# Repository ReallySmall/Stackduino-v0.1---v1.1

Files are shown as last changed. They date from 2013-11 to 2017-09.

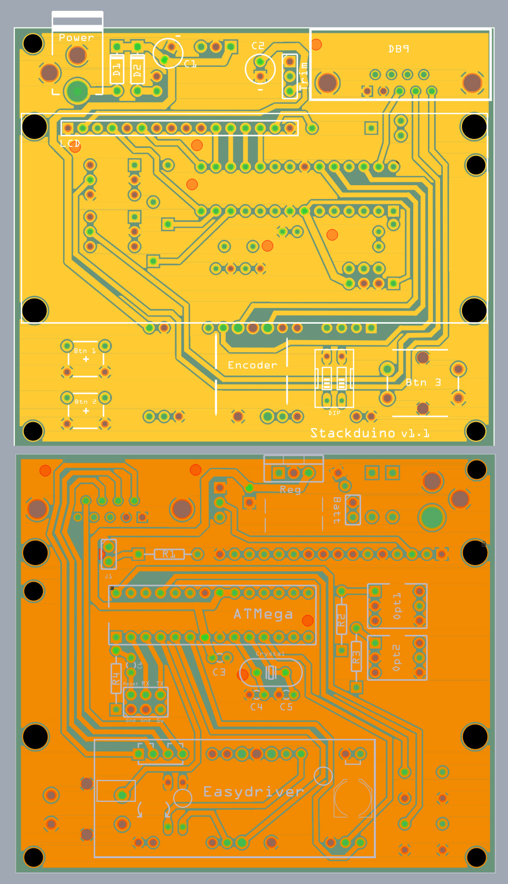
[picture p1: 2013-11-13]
Stackduino-v1.1-pcb-top-bottom-views.jpg

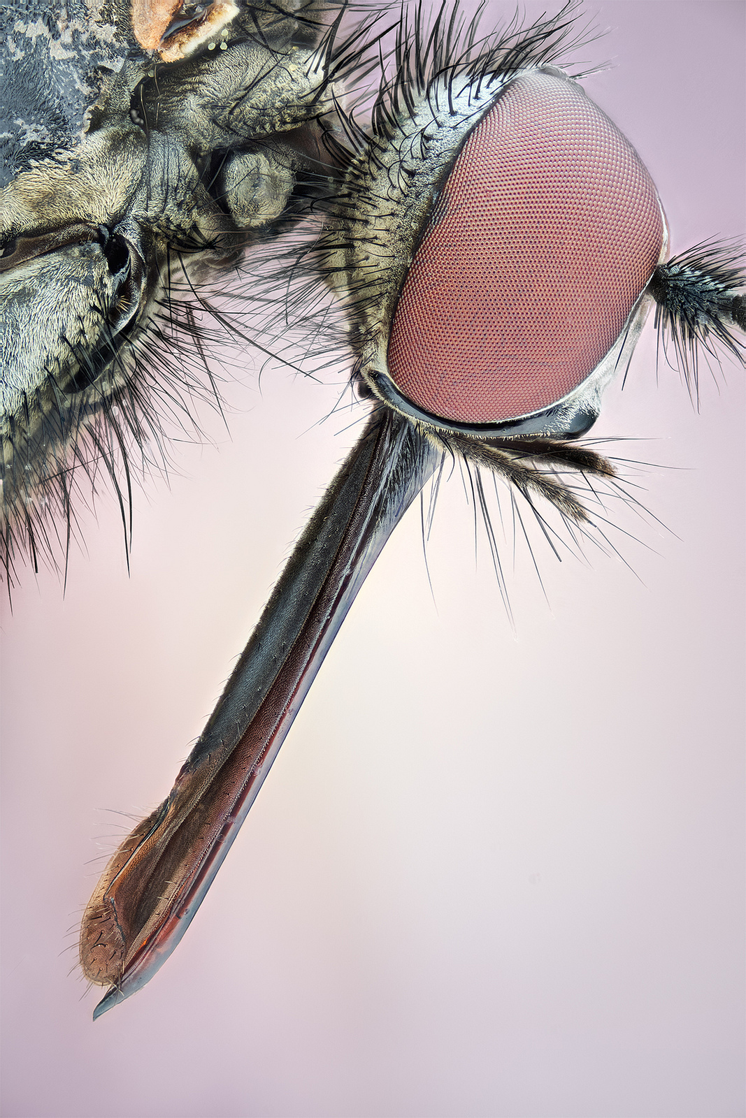
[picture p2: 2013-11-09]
Example image made with Stackduino.jpg

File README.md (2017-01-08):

Stackduino
==========
Please visit the project site for details: https://www.stackduino.net

Copyright 2017 Richard Iles

Permission is hereby granted, free of charge, to any person obtaining a copy of this software and associated documentation files (the "Software"), to deal in the Software without restriction, including without limitation the rights to use, copy, modify, merge, publish, distribute, sublicense, and/or sell copies of the Software, and to permit persons to whom the Software is furnished to do so, subject to the following conditions:

The above copyright notice and this permission notice shall be included in all copies or substantial portions of the Software.

THE SOFTWARE IS PROVIDED "AS IS", WITHOUT WARRANTY OF ANY KIND, EXPRESS OR IMPLIED, INCLUDING BUT NOT LIMITED TO THE WARRANTIES OF MERCHANTABILITY, FITNESS FOR A PARTICULAR PURPOSE AND NONINFRINGEMENT. IN NO EVENT SHALL THE AUTHORS OR COPYRIGHT HOLDERS BE LIABLE FOR ANY CLAIM, DAMAGES OR OTHER LIABILITY, WHETHER IN AN ACTION OF CONTRACT, TORT OR OTHERWISE, ARISING FROM, OUT OF OR IN CONNECTION WITH THE SOFTWARE OR THE USE OR OTHER DEALINGS IN THE SOFTWARE.

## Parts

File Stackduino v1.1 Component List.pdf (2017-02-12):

PCB Component Label | Component Name/ Value | Insert either way? | Notes
Power | DC Barrel Jack Connector | No | 2.1mm centre pole diameter
D1 | Schottky Diode 1A 40v | No | Diode OR power supply select
D2 | Schottky Diode 1A 40v | No | Diode OR power supply select
DB9 | Serial DB9 right angle pcb connector | No | Carries motor, camera and limit switch signals out of the board
C1 | Electrolytic Capacitor 100uF 16v | No | Power supply filtering
C2 | Electrolytic Capacitor 100uF 16v | No | Power supply filtering
C3 | Ceramic Capacitor 0.1uF | Yes | Reset pin
C4 | Ceramic Capacitor 22pf | Yes | Crystal
C5 | Ceramic Capacitor 22pf | Yes | Crystal
C6 | Ceramic Capacitor 0.1uF | Yes | For reset pin when transferring code
Reg | 5v Linear Regulator | No | Voltage regulator
Trim | 10k Trimpot | Yes | LCD contrast control
R1 | 220 Ohm 1/4 Watt Resistor LCD | Yes | LCD backlight
R2 | 220 Ohm 1/4 Watt Resistor | Yes | 4n35 resistor
R3 | 220 Ohm 1/4 Watt Resistor | Yes | 4n35 resistor
R4 | 1.5K Ohm 1/4 Watt Resistor | Yes | Reset pull-up resistor
Opt1 | 4n35 Opto-isolator | No | Camera signal isolation
Opt2 | 4n35 Opto-isolator | No | Camera signal isolation
ATMega | ATMega328 + DIP socket | No | The MCU
Crystal | 16Mhz Crystal | Yes | MCU clock
Easydriver | Easydriver v4.4 Stepper | No | Motor driver
Btn 1 | Mini push button switch | Yes | Manual control - forward
Btn 2 | Mini push button switch | Yes | Manual control - backward
Btn 3 | Push button switch 12mm | Yes | Main function button
Encoder | Standard rotary encoder with push button switch | No | Menu navigation and setting changes
DIP | DIP switch (2 channel) | No | For pulling Easydriver MS1 and MS2 pins high or low
(not labelled) | Male pcb header x 45 | Yes | About 45 male pcb headers needed throughout the board - standard 2.54 pitch

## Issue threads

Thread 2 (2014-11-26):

First image in stack should be taken before stage is moved

ReallySmall, 2014-11-26:
Currently stage moves the first slice distance and then the first image is taken - meaning what you see in the viewfinder/ live view is not quite what gets taken.

ReallySmall, 2017-06-11:
Resolved

Closed 2017-06-11.

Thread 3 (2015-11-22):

Stack not ending is Set Num  over 1

cru67, 2015-11-22:
Hello!
I have a problem. If I put "set num step" on 1 and switch on "return to start", everything like it works shall. Stackudino makes 1 step and a picture and returns into the starting point. I put on "set num step" jump over 1, either no more stop is carried out and a step after the others till I is carried out either the stack breaks off or an end switch is met.

Greetings

ReallySmall, 2015-12-02:
Hello! Sorry for the delay in reply.

I'm puzzled by your being able to set num step to a value of '1' - the minimum value you should be seeing on the screen is '10', and it should increment in multiples of 10.

Can you clarify on that please?
Cheers

cru67, 2015-12-03:
Hello!
Since my English is not so good, I use a translation programme. I hope it is to some extent nevertheless understandable.

Since I have the problem and such a couple of modifications in this have experimented I a little. I am also on this one

working step pushed with the 1 picture.

int slice_depth = 1; //default number of microns stepper motor should make between pictures
int slices = 10; //default total number of pictures to take
int stepper_speed = 1000; //delay in microseconds between motor steps, governing motor speed in stack
int unit_of_measure = 2; //whether to use microns, mm or cm when making steps
int unit_of_measure_multiplier = 1000; //multiplier to factor into step signals (1, 1000 or 10000) depending on unit of measure used
boolean update_screen = true; //whether to print to the lcd with new or updated information

      case 2: //this menu screen changes the number of pictures to take in the stack
        if (rotary_button_state == LOW) { //if rotary encoder button is toggled within a menu, enabled editing of menu variable with encoder
          encoder_update(slices, 1, 5000, 1);
        }

        if (update_screen){  //the screen hardware is slow so only print to it when something changes
          lcd.clear();
          lcd.setCursor(0, 0);
          lcd.print("Set num steps:");
          lcd.setCursor(0, 1);
          lcd_front_load(slices); //frontload with correct number of zeroes and print to screen
          update_screen = false;
        }

        break;

I have the sketch of the Nov 19 2014 with the Arduino version 1.0.5 version tried meanwhile and everything works fine also with the above changes.

Cheers

----- Original Message -----

  From: Richard
  To: ReallySmall/Stackduino-v0.1---v1.1
  Cc: cru67
  Sent: Wednesday, December 02, 2015 6:25 PM
  Subject: Re: [Stackduino-v0.1---v1.1] Stack not ending is Set Num over 1 (#3)

  Hello! Sorry for the delay in reply.

  I'm puzzled by your being able to set num step to a value of '1' - the minimum value you should be seeing on the screen is '10', and it should increment in multiples of 10.

  Can you clarify on that please?
  Cheers

  —
  Reply to this email directly or view it on GitHub.

sanjaykashyap, 2016-01-10:
Hi
cru67,
A very warm happy New Year.
I am unable to get a PCB for Stackduino, so can u help me in buying a
couple of the PCB from the place you have bought.

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

cru67, 2016-01-10:
Hi
Happy New Year to.
I have not bought PCB especially for Stackudino  .I use a Arduino UNO . I have taken something like this  http://www.ebay.de/itm/3x-Strip-Board-PCB-Vero-Prototyping-3-hole-Island-High-Quality-Fast-Delivery-/111573420969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  and built a Shield. Everything in a flying wiring.

ReallySmall, 2016-01-14:
Hi all,

I built an early version in a similar way too: https://www.flickr.com/photos/reallysmall/8387920114/in/album-72157632341602394/

Closed 2016-01-10.

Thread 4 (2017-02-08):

C6 is missing in component list

TinyRbrt, 2017-02-08:
Capacitor C6 is missing in the list of components

ReallySmall, 2017-02-12:
Thanks for highlighting that TinyRbrt 👍

Closed 2017-02-12.

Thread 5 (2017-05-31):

Components

sanjaykashyap, 2017-05-31:
I recently acquire the stackduino v1.1board but I am confused about the Reset, Tx, RX and gnd ,gnd and 5v connection

ReallySmall, 2017-05-31:
Hi,

The purpose of those header pins is to connect a RS232 TTL convertor - e.g: http://www.dx.com/p/pl2303hx-usb-to-rs232-ttl-converter-adapter-module-164590#.WS8BcmjyvIU

That enables you to load the code onto the microcontroller from your pc.

sanjaykashyap, 2017-05-31:
Thanks for your quick response,
I would also like to get advised on how to load the code to the microcontroller as I am not an expert in electronics instead only a biginer.

sanjaykashyap, 2017-06-03:
Hello sir, I have completed the circuit board with all the components and use a 12V 1.5A power supply to light up the circuit. It is all good but the red light in the driver board and the LED display is having small blinking effect. I have not yet load the code on the ATmega 328. Pls advice me on how to load the code.

ReallySmall, 2017-06-11:
Hi,

Sorry for delay in reply - did you make any progress with your issue?

sanjaykashyap, 2017-06-18:
No sir I am stuck where I was, only today I received my USB to serial converter. Moreover may be I have bought the chip ATMEGA 328P without the boot loader. Because of which I am unable to load the programme using a arduino uno board

sanjaykashyap, 2017-06-18:
Sir as I have just received my USB to serial converter, I would like to be advised, on the connections, as per my understanding vcc will go to vcc, ground to ground, RX to TX, and TX to RX, and DTR to Reset. If I am wrong somewhere please correct me. Thanking you

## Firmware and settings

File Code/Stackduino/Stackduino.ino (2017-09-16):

/*////////////////////////////////////////////////////////////////////////////////////////////////////////
//  STACKDUINO 1                                                                                        //
//                                                                                                      //
//  A sketch to drive an Arduino compatible MacroPhotography Focus Stacking Controller                  //
//  http://reallysmall.github.io/Stackduino/                                                            //
//                                                                                                      //
//  KEY HARDWARE:                                                                                       //
//  ATMega 328                                                                                          //
//  Easydriver                                                                                          //
//  Bipolar stepper motor                                                                               //
//  Rotary encoder with momentary push button                                                           //
//  16 x 2 HD44780 lcd                                                                                  //
//  2 x 4n35 optocoupler for camera connection                                                          //
//                                                                                                      //
//  CODE CREDIT:                                                                                        //
//  Reading a rotary encoder - http://www.circuitsathome.com/mcu/reading-rotary-encoder-on-arduino      //   
////////////////////////////////////////////////////////////////////////////////////////////////////////*/

/*////////////////////////////////////////////////////////////////////////////////////////////////////////
//  LIBRARY DEPENDANCIES                                                                                //         
////////////////////////////////////////////////////////////////////////////////////////////////////////*/
#include <LiquidCrystal.h> //LCD library
LiquidCrystal lcd(8, 9, 10, 11, 12, 13); //lcd pins

/*////////////////////////////////////////////////////////////////////////////////////////////////////////
//  ARDUINO PIN ASSIGNMENTS                                                                             //
////////////////////////////////////////////////////////////////////////////////////////////////////////*/

#define ENC_A A0 //rotary encoder (14)
#define ENC_B A1 //rotary encoder (15)
#define ENC_PORT PINC //rotary encoder (a port not a pin)


const byte main_button = 2;  //start/ stop stack button
const byte encoder_button = 3; //select/ unselect menu item button
const byte set_direction = 4; //stepper motor direction
const byte do_step = 5; //send step signal to stepper motor
const byte focus = 6; //send an autofocus signal to the camera
const byte shutter = 7; //send a shutter signal to the camera
const byte forward_control = 16; //for manual positioning
const byte enable = 17; //enable and disable easydriver when not stepping to reduce heat and power consumption (future functionality)
const byte limit_switches = 18; //limit switches to stop stepping if end of travel on rail is reached at either end
const byte backward_control = 19; //for manual positioning

/*////////////////////////////////////////////////////////////////////////////////////////////////////////
//  DEFAULT SETTINGS                                                                                    // 
////////////////////////////////////////////////////////////////////////////////////////////////////////*/
int bracket = 1; //number of images to bracket per focus slice
boolean disable_easydriver = true; //whether to disable easydriver betweem steps to save power and heat
int encoder_counter = 0; //count pulses from encoder
int encoder_pos = 1; //which menu item to display when turning rotary encoder
boolean forward = true; //store the current direction of travel - used when a limit switch is hit because we can't digitalRead the direction pin as it is set as an OUTPUT
int mirror_lockup = 1; //set to 2 to enable mirror lockup
int return_to_start = 1; //whether camera/ subject is returned to starting position at end of stack - set to 2 for yes
int set_pause = 5000; //default time in millis to wait for camera to take picture
int slice_counter = 0; //count of number of pictures taken so far
int slice_depth = 10; //default number of microns stepper motor should make between pictures
int slices = 10; //default total number of pictures to take
int stepper_speed = 2000; //delay in microseconds between motor steps, governing motor speed in stack
int unit_of_measure = 1; //whether to use microns, mm or cm when making steps
int unit_of_measure_multiplier = 1; //multiplier to factor into step signals (1, 1000 or 10,000) depending on unit of measure used
boolean update_screen = true; //whether to print to the lcd with new or updated information

//main button toggle
volatile int main_button_state = HIGH; //the current state of the output pin
volatile int main_button_reading; //the current reading from the input pin
volatile int main_button_previous = LOW; //the previous reading from the input pin
volatile long main_button_time = 0; //the last time the output pin was toggled
volatile long main_button_debounce = 400; //the debounce time, increase if the output flickers

//rotary pushButton toggle
volatile int rotary_button_state = HIGH; //the current state of the output pin
volatile int rbreading; //the current reading from the input pin
volatile int rbprevious = LOW; //the previous reading from the input pin
volatile long rbtime = 0; //the last time the output pin was toggled
volatile long rbdebounce = 400; //the debounce time, increase if the output flickers

/*////////////////////////////////////////////////////////////////////////////////////////////////////////
//  SET PIN FUNCTIONS AND INITIAL STATES, START SERVICES AND PRINT STARTUP MESSAGE                      //    
////////////////////////////////////////////////////////////////////////////////////////////////////////*/
void setup() 

{

  lcd.begin(16, 2);
  Serial.begin(9600);  

  attachInterrupt(0, button_main_change, CHANGE);  //main button on interrupt 0
  attachInterrupt(1, button_rotary_change, CHANGE);  //encoder button on interrupt 1

  pinMode(main_button, INPUT);
  pinMode(encoder_button, INPUT);
  pinMode(set_direction, OUTPUT);   
  pinMode(do_step, OUTPUT);
  pinMode(focus, OUTPUT); 
  pinMode(shutter, OUTPUT);  
  pinMode(ENC_A, INPUT);
  pinMode(ENC_B, INPUT);
  pinMode(forward_control, INPUT); 
  pinMode(enable, OUTPUT);
  pinMode(limit_switches, INPUT);
  pinMode(backward_control, INPUT); 
   
  digitalWrite(main_button, HIGH);
  digitalWrite(encoder_button, HIGH);
  digitalWrite(set_direction, HIGH);
  digitalWrite(do_step, LOW);
  digitalWrite(focus, LOW);
  digitalWrite(shutter, LOW);
  digitalWrite(ENC_A, HIGH);
  digitalWrite(ENC_B, HIGH);
  digitalWrite(forward_control, HIGH);
  digitalWrite(enable, LOW);
  digitalWrite(limit_switches, HIGH);
  digitalWrite(backward_control, HIGH);

  lcd.setCursor(0, 0);
  lcd.print("Stackduino");
  delay(1000);
  lcd.clear();

}

/*////////////////////////////////////////////////////////////////////////////////////////////////////////
//  BUTTON FUNCTIONS                                                                                    //       
////////////////////////////////////////////////////////////////////////////////////////////////////////*/ 

void button_main_change(){ /* RETURN CURRENT STATE OF MAIN PUSH BUTTON */

  main_button_reading = digitalRead(main_button);

  if (main_button_reading == LOW && main_button_previous == HIGH && millis() - main_button_time > main_button_debounce) {
    if (main_button_state == HIGH)
    main_button_state = LOW;
    else
    main_button_state = HIGH;

    main_button_time = millis();    
  }

  main_button_previous = main_button_reading;
} 

void button_rotary_change(){/* RETURN CURRENT STATE OF ROTARY ENCODER'S PUSH BUTTON */

  rbreading = digitalRead(encoder_button);
  if (rbreading == LOW && rbprevious == HIGH && millis() - rbtime > rbdebounce) {
    if (rotary_button_state == HIGH)
    rotary_button_state = LOW;
    else
    rotary_button_state = HIGH;
    rbtime = millis();    
  }

  rbprevious = rbreading;

}

/*////////////////////////////////////////////////////////////////////////////////////////////////////////
//  CAMERA INTERFACE FUNCTIONS                                                                          //       
////////////////////////////////////////////////////////////////////////////////////////////////////////*/ 

void camera_process_images(){ /* SEND SIGNAL TO CAMERA TO TAKE PICTURE WITH DELAYS TO ALLOW SETTLING */
  for (int i = 1; i <= bracket; i++)
  {
    lcd.clear();
    if(bracket > 1){ //if bracketing is enabled, print the current position in the bracket
      lcd.print("Bracketed image:");
      lcd.setCursor(0, 1);
      lcd.print(i);
      lcd.print(" of ");
      lcd.print(bracket);
      delay(1000);
      lcd.clear();
    }
    
    camera_shutter_signal(); //send a shutter signal
       
    lcd.print("Pause for image");
    lcd.setCursor(0, 1);
    lcd.print("(");
    lcd.print ((set_pause / 1000), DEC);
    lcd.print(" seconds)");

    delay(set_pause); //pause to allow for camera to take picture and to allow flashes to recharge before next shot

    lcd.clear();
  }
}

void camera_shutter_signal() { /* SEND SHUTTER SIGNAL */ 
  for (int i = 0; i < mirror_lockup; i++)
  {

    if(mirror_lockup == 2 && i == 0){
      lcd.clear();
      lcd.print("Mirror up");
    }

    digitalWrite(focus, HIGH); //trigger camera autofocus - camera may not take picture in some modes if this is not triggered first
    digitalWrite(shutter, HIGH); //trigger camera shutter

    delay(200); //small delay needed for camera to process above signals

    digitalWrite(shutter, LOW); //switch off camera trigger signal
    digitalWrite(focus, LOW); //switch off camera focus signal

    if(mirror_lockup == 2 && i == 0){
      delay(2000); //sets the delay between mirror up and shutter
      lcd.clear();
    }
  }
}

/*////////////////////////////////////////////////////////////////////////////////////////////////////////
//  ROTARY ENCODER FUNCTIONS                                                                            //       
////////////////////////////////////////////////////////////////////////////////////////////////////////*/  

int8_t encoder_read(){ /* RETURN CHANGE IN ENCODER STATE */

  static int8_t enc_states[] = { 
    //0,1,-1,0,-1,0,0,1,1,0,0,-1,0,-1,1,0 //use this line instead to increment encoder in the opposite direction
    0,-1,1,0,1,0,0,-1,-1,0,0,1,0,1,-1,0
  };
  static uint8_t old_AB = 0;
  /**/
  old_AB <<= 2; //remember previous state
  old_AB |= ( ENC_PORT & 0x03 ); //add current state
  return ( enc_states[( 0x0f & old_AB )]);

}

void encoder_update(int &variable, int lower, int upper, int multiplier = 1){ /* CHANGE THE ACTIVE MENU VARIABLE'S VALUE USING THE ENCODER */
  
  variable = constrain(variable, lower, upper); //keep variable value within specified range  
  
  int8_t encoder_data = encoder_read(); //counts encoder pulses and registers only every nth pulse to adjust feedback sensitivity
  
  if(encoder_data){
    if(encoder_data == 1){
      encoder_counter++;
    }

    if(encoder_counter == 2){ //change this number to adjust encoder sensitivity 4 or 2 are usually the values to use
      variable = variable + multiplier;
      update_screen = true; //as a variable has just been changed by the encoder, flag the screen as updatable
      encoder_counter = 0;
    }

    if(encoder_data == -1){
      encoder_counter--;
    }
    if(encoder_counter == -2){ //change this number to adjust encoder sensitivity 4 or 2 are usually the values to use
      variable = variable - multiplier;
      update_screen = true; //as a variable has just been changed by the encoder, flag the screen as updatable
      encoder_counter = 0;
    }
  }

}

/*////////////////////////////////////////////////////////////////////////////////////////////////////////
//  LCD DISPLAY FORMATTING FUNCTIONS                                                                    //       
////////////////////////////////////////////////////////////////////////////////////////////////////////*/  

void lcd_front_load(int variable) { /* FRONT PAD MENU ITEM NUMBERS WITH ZEROES */
  if (variable < 10){
    lcd.print (000, DEC); //adds three leading zeros to single digit Step size numbers on the display
  }
  if (variable < 100){
    lcd.print (00, DEC); //adds two leading zeros to double digit Step size numbers on the display
  }
  if (variable < 1000){
    lcd.print (0, DEC); //adds one leading zero to triple digit Step size numbers on the display
  }
  lcd.print(variable, DEC);
}

void lcd_unit_of_measure() { /* PRINT SELECTED UNIT OF MEASURE TO SCREEN */        
  if (unit_of_measure==1){
    lcd.print(" mn");
  }
  if (unit_of_measure==2){
    lcd.print(" mm");
  }
  if (unit_of_measure==3){
    lcd.print(" cm");
  }
}

/*////////////////////////////////////////////////////////////////////////////////////////////////////////
//  STEPPER MOTOR CONTROL FUNCTIONS                                                                     //       
////////////////////////////////////////////////////////////////////////////////////////////////////////*/

void stepper_control(){ /* MOVE CARRIAGE BACKWARD AND FORWARD MANUALLY USING PUSH BUTTONS */

  while (digitalRead(forward_control) == LOW) {
    stepper_enable();
    digitalWrite(set_direction, HIGH);
    forward = true; 
    for (int i = 0; i<1; i++)
    {
      stepper_step(); //move forward
    }
    stepper_disable();
  }

  while (digitalRead(backward_control) == LOW) {
    stepper_enable();
    digitalWrite(set_direction, LOW);
    forward = false; 
    for (int i = 0; i<1; i++)
    {
      stepper_step(); //move backward
    }
    stepper_disable();
  }

}

void stepper_direction(){ /* REVERSE THE CURRENT STEPPER DIRECTION */
  if(forward){
      digitalWrite(set_direction, LOW);
      forward = false;
    } else {
      digitalWrite(set_direction, HIGH);
      forward = true;
    }
}

void stepper_disable() { /* DISABLE THE EASYDRIVER WHEN NOT IN USE IF OPTION SET */
  if(disable_easydriver == true) {
    digitalWrite(enable, HIGH);
  } 
  else {
    digitalWrite(enable, LOW);
  } 
}

void stepper_enable() { /* ENABLE THE EASYDRIVER */
  digitalWrite(enable, LOW);
}

void stepper_retreat(){ /* PULL CARRIAGE BACK FROM TRIPPED LIMIT SWITCH */
  stepper_enable();
  stepper_direction(); //switch the motor direction
  lcd.clear();
  lcd.setCursor(0, 0);
  lcd.print("End of travel!");
  lcd.setCursor(0, 1);
  lcd.print("Reversing...");

  while (digitalRead(limit_switches) == LOW) //iterate do_step signal for as long as eitherlimit switch remains pressed 
  {  
    stepper_step();
  }

  stepper_direction(); //reset motor back to original direction once limit switch is no longer pressed
  lcd.clear();
  stepper_disable();
}

void stepper_step(){ /* SEND A STEP SIGNAL TO EASYDRIVER TO TURN MOTOR */

  digitalWrite(do_step, LOW); //this LOW to HIGH change is what creates the
  digitalWrite(do_step, HIGH); //"Rising Edge" so the easydriver knows to when to step
  delayMicroseconds(stepper_speed); //delay time between steps, too fast and motor stalls

}

void loop(){

/*////////////////////////////////////////////////////////////////////////////////////////////////////////
//  CHECK A LIMIT SWITCH ISN'T TRIPPED ON STARTUP                                                       //     
////////////////////////////////////////////////////////////////////////////////////////////////////////*/
  if (digitalRead(limit_switches) == LOW){ //if controller is started up hitting a limit switch disable main functions and print warning to lcd
    stepper_disable(); //disable easydriver

    lcd.clear();
    lcd.setCursor(0, 0);
    lcd.print("End of travel!");
    lcd.setCursor(0, 1); 

    stepper_control(); //Provide manual motor control to move away from limit switch and resolve error
  }
  else{ //if limit switches HIGH run all functions normally

    if (main_button_state == HIGH){
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

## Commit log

2013-03-03 added Fritzing wiring diagram
    [Stackduino-160213.fzz]
2013-03-03 Chnaged file name
    [Stackduino-fritzing-wiring-diagram.fzz]
2013-06-30 Removed old files
    [Stackduino-fritzing-wiring-diagram.fzz]
2013-10-12 Updated direction code to match wiring of pcb
2013-11-09 Added gereber files for Stackduino v1.1
    [stackduino-pcb-rev-1.1_contour.gm1, stackduino-pcb-rev-1.1_copperBottom.gbl, stackduino-pcb-rev-1.1_copperTop.gtl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]
2013-11-09 Added pcb diagram
2013-11-10 Enabled option to disable Easydriver
    ...when not stepping. Runs a lot cooler and uses less power
2013-11-12 added pcb component labels
    [stackduino-pcb-rev-1.1_copperBottom.gbl, stackduino-pcb-rev-1.1_copperTop.gtl, stackduino-pcb-rev-1.1_maskBottom.gbs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]
2013-11-12 Added silkscreen labels
    [stackduino-pcb-rev-1.1_copperTop.gtl, stackduino-pcb-rev-1.1_silkBottom.gbo, stackduino-pcb-rev-1.1_silkTop.gto]
2013-11-17 Added HDR bracketing support
    Stackduino can take a selectable multiple of images per focus slice to
    support exposure bracketing
2014-07-13 Overhauled sketch
    - no longer requires the DigitalToggle library
    - screen updates are done more effeciently, only when variables are
    changed - and the check is now done once diectly within the encoder
    reading function, rather than individually within each menu item
    - due to more efficient screen updates, lcd.clear can now be used before
    each update, so padding out strings to fill lcd rows is no longer
    necessary
    - added mirror lockup support - sends two delay seprated shutter signals
    [Stackduino.ino]
2014-07-20 Started Stackduino v1.2 board in Eagle
    [Stackduino.brd, Stackduino.sch]
2014-11-19 corrected error in component list
    [Stackduino.sch, Stackduino_v1.2_beta.brd, Stackduino_v1.2_beta.sch]
2014-11-19 reinstated correct sketch
    Woops!
    [Stackduino.ino]
2015-09-26 Fixed compile error in newest version of IDE
    [Stackduino.ino]
2017-01-08 Folder tidyup
    [Stackduino_v1.2_beta.brd, Stackduino_v1.2_beta.sch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]
2017-09-16 fix overwriting of parent loop variable
    [Stackduino.ino]
